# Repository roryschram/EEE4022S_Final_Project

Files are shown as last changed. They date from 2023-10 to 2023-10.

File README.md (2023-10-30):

## LoRa Based Communication System for Radiosonde Applications
### By Rory Schram

Welcome to my final year project GitHub page. This project focussed on the design and implementation of a LoRa-based radiosonde module for a weather balloon. Project files can be found in their respective folders, including all software, schematics, and PCB designs, for the transmission and receiver modules.

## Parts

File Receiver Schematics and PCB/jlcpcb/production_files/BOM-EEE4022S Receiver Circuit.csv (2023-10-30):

Comment | Designator | Footprint | LCSC
~ | U1 | ESP8266
~ | U4 | SX1278
Navigator Button | U2 | Push Button
~ | U5 | OLED Display

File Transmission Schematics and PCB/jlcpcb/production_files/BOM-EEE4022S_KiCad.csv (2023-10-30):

Comment | Designator | Footprint | LCSC
~ | U5 | FTDI
~ | U3 | NEO-6M
Left Button | U6 | Push Button
~ | U4 | BME280
Right Button | U7 | Push Button
~ | B1 | Battery HolderCharger
~ | U1 | STM32f4_Black_Pill
~ | U8 | OLED Display
~ | U2 | SX1278

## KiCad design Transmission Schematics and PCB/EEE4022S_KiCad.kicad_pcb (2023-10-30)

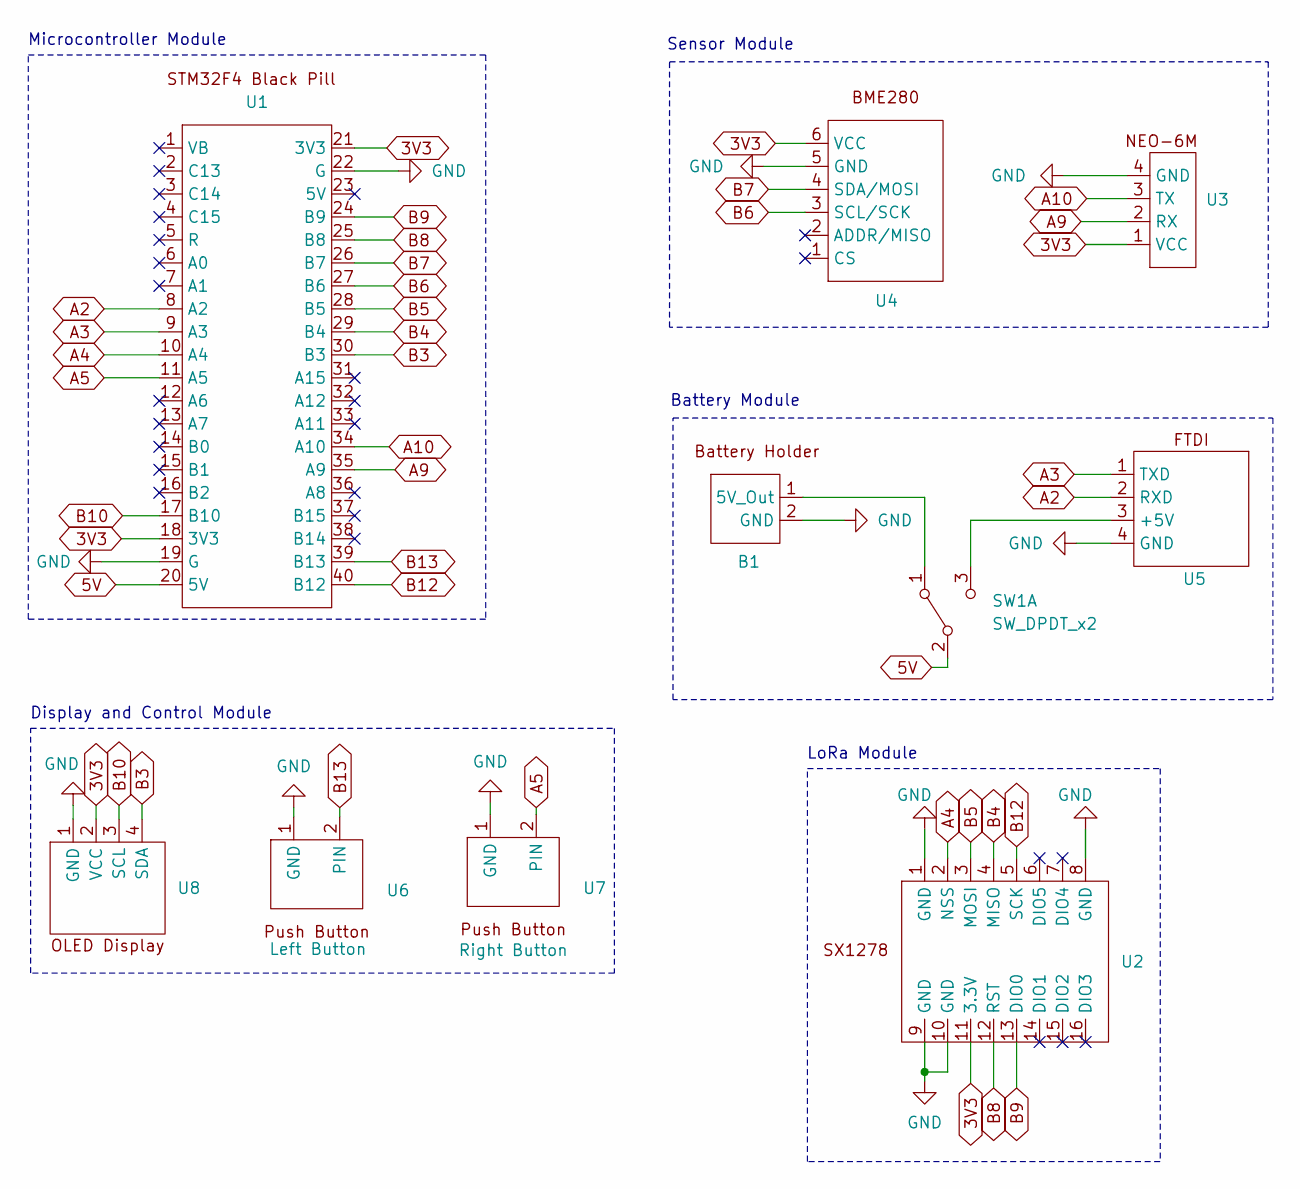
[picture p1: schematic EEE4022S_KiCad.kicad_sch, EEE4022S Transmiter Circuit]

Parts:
B1: Battery HolderCharger
SW1: SW_DPDT_x2
U1: STM32f4_Black_Pill
U2: SX1278
U3: NEO-6M
U4: BME280
U5: FTDI
U6: Left Button; Push Button
U7: Right Button; Push Button
U8: OLED Display

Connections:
3V3: U1.18 (3V3), U1.21 (3V3), U2.11 (3.3V), U3.1 (VCC), U4.6 (VCC), U8.2 (VCC)
5V: B1.1 (5V_Out), SW1.1 (A), SW1.2 (B), SW1.3 (C), U1.20 (5V), U5.3 (+5V)
A2: U1.8 (A2), U5.2 (RXD)
A3: U1.9 (A3), U5.1 (TXD)
A4: U1.10 (A4), U2.2 (NSS)
A5: U1.11 (A5), U7.2 (PIN)
A9: U1.35 (A9), U3.2 (RX)
A10: U1.34 (A10), U3.3 (TX)
B3: U1.30 (B3), U8.4 (SDA)
B4: U1.29 (B4), U2.4 (MISO)
B5: U1.28 (B5), U2.3 (MOSI)
B6: U1.27 (B6), U4.3 (SCL/SCK)
B7: U1.26 (B7), U4.4 (SDA/MOSI)
B8: U1.25 (B8), U2.12 (RST)
B9: U1.24 (B9), U2.13 (DIO0)
B10: U1.17 (B10), U8.3 (SCL)
B12: U1.40 (B12), U2.5 (SCK)
B13: U1.39 (B13), U6.2 (PIN)
GND: B1.2 (GND), U1.19 (G), U1.22 (G), U2.1 (GND), U2.8 (GND), U2.9 (GND), U2.10 (GND), U3.4 (GND), U4.5 (GND), U5.4 (GND), U6.1 (GND), U7.1 (GND), U8.1 (GND)

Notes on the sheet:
LoRa Module
Display and Control Module
Sensor Module
Microcontroller Module
Battery Module

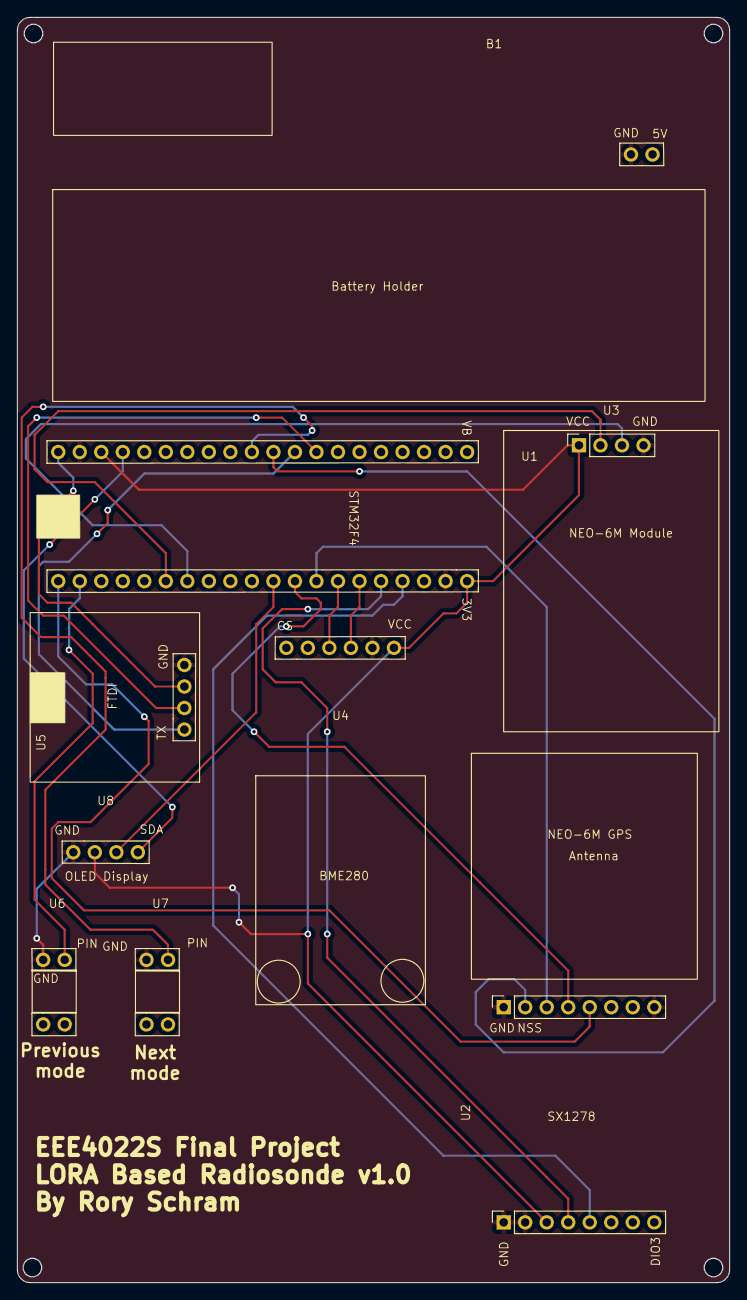
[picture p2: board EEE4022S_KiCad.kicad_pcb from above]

Board: 2 copper layers, 84.1 x 149.4 mm, 9 parts (0 on the bottom side), 19 nets.

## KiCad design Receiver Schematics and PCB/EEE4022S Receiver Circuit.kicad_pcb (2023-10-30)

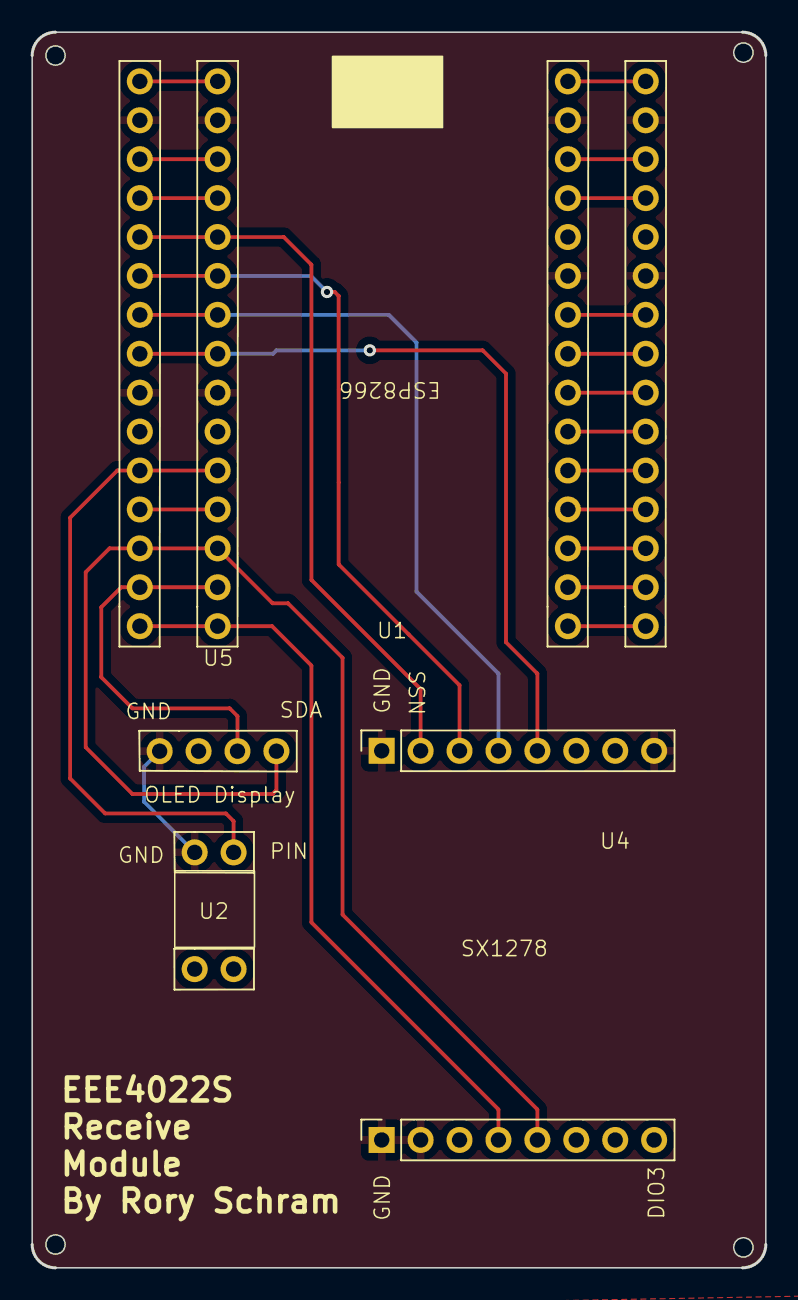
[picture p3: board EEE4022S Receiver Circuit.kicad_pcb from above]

Board: 2 copper layers, 47.9 x 80.6 mm, 4 parts (0 on the bottom side), 10 nets.

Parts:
U1: ESP8266
U2: Navigator Button; Push Button
U4: SX1278
U5: OLED Display

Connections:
3V3: U1.11 (3V3), U1.21 (3V3), U4.11 (3.3V), U5.2 (VCC)
D0: U1.16 (D0), U4.12 (RST)
D1: U1.17 (D1), U5.3 (SCL)
D2: U1.18 (D2), U4.13 (DIO0), U5.4 (SDA)
D4: U1.20 (D4), U2.2 (PIN)
D5: U1.23 (D5), U4.5 (SCK)
D6: U1.24 (D6), U4.4 (MISO)
D7: U1.25 (D7), U4.3 (MOSI)
D8: U1.26 (D8), U4.2 (NSS)
GND: U1.10 (GND), U1.14 (GND), U1.22 (GND), U1.29 (GND), U2.1 (GND), U4.1 (GND), U4.8 (GND), U4.9 (GND), U4.10 (GND), U5.1 (GND)

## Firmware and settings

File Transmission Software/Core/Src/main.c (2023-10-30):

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
/* Includes ------------------------------------------------------------------*/
#include "main.h"

/* USER CODE BEGIN Includes */
#include <stdio.h>
#include "minmea.h"
#include <stdlib.h>
#include <string.h>
#include <stdint.h>
#include "bmp280.h"
#include <float.h>
#include <math.h>
#include <LoRa.h>
#include "ssd1306.h"
#include "fonts.h"


/* USER CODE END Includes */

/* USER CODE BEGIN PD */
#define INDENT_SPACES "  "

/* USER CODE END PD */

I2C_HandleTypeDef hi2c1;
I2C_HandleTypeDef hi2c2;

SPI_HandleTypeDef hspi3;

TIM_HandleTypeDef htim3;

UART_HandleTypeDef huart1;
UART_HandleTypeDef huart2;

/* USER CODE BEGIN PV */
uint8_t gps_raw[512] = {"\0"};
uint8_t flag = 0;
char line[64] = {"\0"};
bool bme280p;
uint8_t transmit_data[256] = {"\0"};
LoRa myLoRa;
bool isLoraReady = true;
int preTicks = 0;
int currentTicks = 0;
int iMode = 1;
char sMode[10];
bool bModeChanged = true;
bool sendData = false;


bool beginTransmit = false;
uint16_t packetSize = 0;

//Variables to work out altitude

//Pressure at sea level
float P_b = 101325;

//Height that we are calculating
float altitude = 0;


BMP280_HandleTypedef bmp280;

float pressure, temperature, humidity;
char sPressure[128] = {"\0"};
char sTemperature[128] = {"\0"};
char sHumidity[128] = {"\0"};
char sAltitude[128] = {"\0"};

size_t size;
uint8_t Data[256] = {"\0"};


/* USER CODE END PV */

void SystemClock_Config(void);
static void MX_GPIO_Init(void);
static void MX_USART1_UART_Init(void);
static void MX_USART2_UART_Init(void);
static void MX_I2C1_Init(void);
static void MX_SPI3_Init(void);
static void MX_I2C2_Init(void);
static void MX_TIM3_Init(void);
/* USER CODE BEGIN PFP */
uint16_t buildDataPacket();


/* USER CODE END PFP */

/**
  * @brief  The application entry point.
  * @retval int
  */
int main(void)
{
  /* MCU Configuration--------------------------------------------------------*/

  /* Reset of all peripherals, Initializes the Flash interface and the Systick. */
  HAL_Init();

  /* Configure the system clock */
  SystemClock_Config();

  /* Initialize all configured peripherals */
  MX_GPIO_Init();
  MX_USART1_UART_Init();
  MX_USART2_UART_Init();
  MX_I2C1_Init();
  MX_SPI3_Init();
  MX_I2C2_Init();
  MX_TIM3_Init();
  /* USER CODE BEGIN 2 */
  
  // Start timer
  HAL_TIM_Base_Start_IT(&htim3);

  bmp280_init_default_params(&bmp280.params);
	bmp280.addr = 0x77;
	bmp280.i2c = &hi2c1;

	while (!bmp280_init(&bmp280, &bmp280.params)) {
		size = sprintf((char *)Data, "BMP280 initialization failed\n");
		HAL_UART_Transmit(&huart2, Data, size, 1000);
		HAL_Delay(2000);
	}
	bool bme280p = bmp280.id == BME280_CHIP_ID;
	size = sprintf((char *)Data, "\nBMP280: found %s\n", bme280p ? "BME280" : "BMP280");
	HAL_UART_Transmit(&huart2, Data, size, 1000);

  myLoRa = newLoRa();
  myLoRa.CS_port         = GPIOA;
  myLoRa.CS_pin          = GPIO_PIN_4;
  myLoRa.reset_port      = GPIOB;
  myLoRa.reset_pin       = GPIO_PIN_8;
  myLoRa.DIO0_port       = GPIOB;
  myLoRa.DIO0_pin        = GPIO_PIN_9;
  myLoRa.hSPIx           = &hspi3;
  
  
  myLoRa.frequency             = 433;             // default = 433 MHz
  myLoRa.spreadingFactor        = SF_7;            // default = SF_7
  myLoRa.bandWidth             = BW_7_8KHz;       // default = BW_125KHz
  myLoRa.crcRate               = CR_4_5;          // default = CR_4_5
  myLoRa.power                 = POWER_20db;      // default = 20db
  myLoRa.overCurrentProtection = 100;             // default = 100 mA
  myLoRa.preamble              = 8;              // default = 8;

  uint16_t ret = LoRa_init(&myLoRa);
  uint8_t buff[128] = {"\0"};
  

if (ret==LORA_OK){
  snprintf(buff,sizeof(buff),"LoRa is running... :) \n\r");
  size = strlen(&buff);
  LoRa_transmit(&myLoRa, (uint8_t*)buff, size, 100);
  HAL_UART_Transmit_IT(&huart2, buff, size);
}
else{
  snprintf(buff,sizeof(buff),"\n\r LoRa failed :( \n\r Error code: %d \n\r", ret);
  size = strlen(&buff);
  HAL_UART_Transmit_IT(&huart2, buff, size);
}


ssd1306_Init(&hi2c2);

// Set cursors and write the word "mode"
ssd1306_SetCursor(0, 0);
ssd1306_WriteString("Mode:", Font_16x26, White);

ssd1306_SetCursor(0, 35);
sprintf(sMode, "%d", iMode);
ssd1306_WriteString(sMode, Font_16x26, White);

// Copy all data from local screenbuffer to the screen
ssd1306_UpdateScreen(&hi2c2);

HAL_UARTEx_ReceiveToIdle(&huart1,(uint8_t*)gps_raw,512,512,1000);


  /* USER CODE END 2 */

  /* Infinite loop */
  /* USER CODE BEGIN WHILE */
  while (1)
  {


    if (beginTransmit) {
      //HAL_UART_Transmit(&huart2,(uint8_t *)gps_raw,512, 1000);
      //HAL_UARTEx_ReceiveToIdle_IT(&huart1,(uint8_t*)gps_raw,512);
      packetSize = buildDataPacket();
      
      size = strlen(&transmit_data);
      ret = LoRa_transmit(&myLoRa, (uint8_t*)transmit_data, packetSize, 10000);
      memset(transmit_data, '\0', sizeof(transmit_data));

      // sprintf(transmit_data, "Data sent with code %u\n", ret);
      // size = strlen(&transmit_data);
	    // HAL_UART_Transmit(&huart2, (uint8_t *)transmit_data, size, 1000);
      // memset(transmit_data, '\0', sizeof(transmit_data));
      
      beginTransmit = false;
    }      

    if (bModeChanged) {
switch (iMode) {
    case 1:
      // statements
      myLoRa.frequency             = 433;             // default = 433 MHz
      myLoRa.spreadingFactor        = SF_7;            // default = SF_7
      myLoRa.bandWidth             = BW_7_8KHz;       // default = BW_125KHz
      myLoRa.crcRate               = CR_4_5;          // default = CR_4_5
      myLoRa.power                 = POWER_20db;      // default = 20db
      myLoRa.overCurrentProtection = 100;             // default = 100 mA
      myLoRa.preamble              = 8;              // default = 8;
      LoRa_init(&myLoRa);
      break;

    case 2:
      // statements
      myLoRa.frequency             = 433;             // default = 433 MHz
      myLoRa.spreadingFactor        = SF_7;            // default = SF_7
      myLoRa.bandWidth             = BW_10_4KHz;       // default = BW_125KHz
      myLoRa.crcRate               = CR_4_5;          // default = CR_4_5
      myLoRa.power                 = POWER_20db;      // default = 20db
      myLoRa.overCurrentProtection = 100;             // default = 100 mA
      myLoRa.preamble              = 8;              // default = 8;
      LoRa_init(&myLoRa);
      break;

    case 3:
      // statements
      myLoRa.frequency             = 433;             // default = 433 MHz
      myLoRa.spreadingFactor        = SF_7;            // default = SF_7
      myLoRa.bandWidth             = BW_15_6KHz;       // default = BW_125KHz
      myLoRa.crcRate               = CR_4_5;          // default = CR_4_5
      myLoRa.power                 = POWER_20db;      // default = 20db
      myLoRa.overCurrentProtection = 100;             // default = 100 mA
      myLoRa.preamble              = 8;              // default = 8;
      LoRa_init(&myLoRa);
      break;

    case 4:
      // statements
      myLoRa.frequency             = 433;             // default = 433 MHz
      myLoRa.spreadingFactor        = SF_7;            // default = SF_7
      myLoRa.bandWidth             = BW_20_8KHz;       // default = BW_125KHz
      myLoRa.crcRate               = CR_4_5;          // default = CR_4_5
      myLoRa.power                 = POWER_20db;      // default = 20db
      myLoRa.overCurrentProtection = 100;             // default = 100 mA
      myLoRa.preamble              = 8;              // default = 8;
      LoRa_init(&myLoRa);
      break;

    case 5:
      // statements
      myLoRa.frequency             = 433;             // default = 433 MHz
      myLoRa.spreadingFactor        = SF_7;            // default = SF_7
      myLoRa.bandWidth             = BW_31_25KHz;       // default = BW_125KHz
      myLoRa.crcRate               = CR_4_5;          // default = CR_4_5
      myLoRa.power                 = POWER_20db;      // default = 20db
      myLoRa.overCurrentProtection = 100;             // default = 100 mA
      myLoRa.preamble              = 8;              // default = 8;
      LoRa_init(&myLoRa);
      break;

    case 6:
      // statements
      myLoRa.frequency             = 433;             // default = 433 MHz
      myLoRa.spreadingFactor        = SF_7;            // default = SF_7
      myLoRa.bandWidth             = BW_41_7KHz;       // default = BW_125KHz
      myLoRa.crcRate               = CR_4_5;          // default = CR_4_5
      myLoRa.power                 = POWER_20db;      // default = 20db
      myLoRa.overCurrentProtection = 100;             // default = 100 mA
      myLoRa.preamble              = 8;              // default = 8;
      LoRa_init(&myLoRa);
      break;

    case 7:
      // statements
      myLoRa.frequency             = 433;             // default = 433 MHz
      myLoRa.spreadingFactor        = SF_7;            // default = SF_7
      myLoRa.bandWidth             = BW_62_5KHz;       // default = BW_125KHz
      myLoRa.crcRate               = CR_4_5;          // default = CR_4_5
      myLoRa.power                 = POWER_20db;      // default = 20db
      myLoRa.overCurrentProtection = 100;             // default = 100 mA
      myLoRa.preamble              = 8;              // default = 8;
      LoRa_init(&myLoRa);
      break;

    case 8:
      // statements
      myLoRa.frequency             = 433;             // default = 433 MHz
      myLoRa.spreadingFactor        = SF_7;            // default = SF_7
      myLoRa.bandWidth             = BW_125KHz;       // default = BW_125KHz
      myLoRa.crcRate               = CR_4_5;          // default = CR_4_5
      myLoRa.power                 = POWER_20db;      // default = 20db
      myLoRa.overCurrentProtection = 100;             // default = 100 mA
      myLoRa.preamble              = 8;              // default = 8;
      LoRa_init(&myLoRa);
      break;

    case 9:
      // statements
      myLoRa.frequency             = 433;             // default = 433 MHz
      myLoRa.spreadingFactor        = SF_7;            // default = SF_7
      myLoRa.bandWidth             = BW_250KHz;       // default = BW_125KHz
      myLoRa.crcRate               = CR_4_5;          // default = CR_4_5
      myLoRa.power                 = POWER_20db;      // default = 20db
      myLoRa.overCurrentProtection = 100;             // default = 100 mA
      myLoRa.preamble              = 8;              // default = 8;
      LoRa_init(&myLoRa);
      break;

    case 10:
      // statements
      myLoRa.frequency             = 433;             // default = 433 MHz
      myLoRa.spreadingFactor        = SF_7;            // default = SF_7
      myLoRa.bandWidth             = BW_500KHz;       // default = BW_125KHz
      myLoRa.crcRate               = CR_4_5;          // default = CR_4_5
      myLoRa.power                 = POWER_20db;      // default = 20db
      myLoRa.overCurrentProtection = 100;             // default = 100 mA
      myLoRa.preamble              = 8;              // default = 8;
      LoRa_init(&myLoRa);
      break;
    
    case 11:
      // statements
      myLoRa.frequency             = 433;             // default = 433 MHz
      myLoRa.spreadingFactor        = SF_8;            // default = SF_7
      myLoRa.bandWidth             = BW_7_8KHz;       // default = BW_125KHz
      myLoRa.crcRate               = CR_4_5;          // default = CR_4_5
      myLoRa.power                 = POWER_20db;      // default = 20db
      myLoRa.overCurrentProtection = 100;             // default = 100 mA
      myLoRa.preamble              = 8;              // default = 8;
      LoRa_init(&myLoRa);
      break;

    case 12:
      // statements
      myLoRa.frequency             = 433;             // default = 433 MHz
      myLoRa.spreadingFactor        = SF_8;            // default = SF_7
      myLoRa.bandWidth             = BW_10_4KHz;       // default = BW_125KHz
      myLoRa.crcRate               = CR_4_5;          // default = CR_4_5
      myLoRa.power                 = POWER_20db;      // default = 20db
      myLoRa.overCurrentProtection = 100;             // default = 100 mA
      myLoRa.preamble              = 8;              // default = 8;
      LoRa_init(&myLoRa);
      break;

    case 13:
      // statements
      myLoRa.frequency             = 433;             // default = 433 MHz
      myLoRa.spreadingFactor        = SF_8;            // default = SF_7
      myLoRa.bandWidth             = BW_15_6KHz;       // default = BW_125KHz
      myLoRa.crcRate               = CR_4_5;          // default = CR_4_5
      myLoRa.power                 = POWER_20db;      // default = 20db
      myLoRa.overCurrentProtection = 100;             // default = 100 mA
      myLoRa.preamble              = 8;              // default = 8;
      LoRa_init(&myLoRa);
      break;

    case 14:
      // statements
      myLoRa.frequency             = 433;             // default = 433 MHz
      myLoRa.spreadingFactor        = SF_8;            // default = SF_7
      myLoRa.bandWidth             = BW_20_8KHz;       // default = BW_125KHz
      myLoRa.crcRate               = CR_4_5;          // default = CR_4_5
      myLoRa.power                 = POWER_20db;      // default = 20db
      myLoRa.overCurrentProtection = 100;             // default = 100 mA
      myLoRa.preamble              = 8;              // default = 8;
      LoRa_init(&myLoRa);
      break;

    case 15:
      // statements
      myLoRa.frequency             = 433;             // default = 433 MHz
      myLoRa.spreadingFactor        = SF_8;            // default = SF_7
      myLoRa.bandWidth             = BW_31_25KHz;       // default = BW_125KHz
      myLoRa.crcRate               = CR_4_5;          // default = CR_4_5
      myLoRa.power                 = POWER_20db;      // default = 20db
      myLoRa.overCurrentProtection = 100;             // default = 100 mA
      myLoRa.preamble              = 8;              // default = 8;
      LoRa_init(&myLoRa);
      break;

    case 16:
      // statements
      myLoRa.frequency             = 433;             // default = 433 MHz
      myLoRa.spreadingFactor        = SF_8;            // default = SF_7
      myLoRa.bandWidth             = BW_41_7KHz;       // default = BW_125KHz
      myLoRa.crcRate               = CR_4_5;          // default = CR_4_5
      myLoRa.power                 = POWER_20db;      // default = 20db
      myLoRa.overCurrentProtection = 100;             // default = 100 mA
      myLoRa.preamble              = 8;              // default = 8;
      LoRa_init(&myLoRa);
      break;

    case 17:
      // statements
      myLoRa.frequency             = 433;             // default = 433 MHz
      myLoRa.spreadingFactor        = SF_8;            // default = SF_7
      myLoRa.bandWidth             = BW_62_5KHz;       // default = BW_125KHz
      myLoRa.crcRate               = CR_4_5;          // default = CR_4_5
      myLoRa.power                 = POWER_20db;      // default = 20db
      myLoRa.overCurrentProtection = 100;             // default = 100 mA
      myLoRa.preamble              = 8;              // default = 8;
      LoRa_init(&myLoRa);
      break;

    case 18:
      // statements
      myLoRa.frequency             = 433;             // default = 433 MHz
      myLoRa.spreadingFactor        = SF_8;            // default = SF_7
      myLoRa.bandWidth             = BW_125KHz;       // default = BW_125KHz
      myLoRa.crcRate               = CR_4_5;          // default = CR_4_5
      myLoRa.power                 = POWER_20db;      // default = 20db
      myLoRa.overCurrentProtection = 100;             // default = 100 mA
      myLoRa.preamble              = 8;              // default = 8;
      LoRa_init(&myLoRa);
      break;

    case 19:
      // statements
      myLoRa.frequency             = 433;             // default = 433 MHz
      myLoRa.spreadingFactor        = SF_8;            // default = SF_7
      myLoRa.bandWidth             = BW_250KHz;       // default = BW_125KHz
      myLoRa.crcRate               = CR_4_5;          // default = CR_4_5
      myLoRa.power                 = POWER_20db;      // default = 20db
      myLoRa.overCurrentProtection = 100;             // default = 100 mA
      myLoRa.preamble              = 8;              // default = 8;
      LoRa_init(&myLoRa);
      break;

    case 20:
      // statements
      myLoRa.frequency             = 433;             // default = 433 MHz
      myLoRa.spreadingFactor        = SF_8;            // default = SF_7
      myLoRa.bandWidth             = BW_500KHz;       // default = BW_125KHz
      myLoRa.crcRate               = CR_4_5;          // default = CR_4_5
      myLoRa.power                 = POWER_20db;      // default = 20db
      myLoRa.overCurrentProtection = 100;             // default = 100 mA
      myLoRa.preamble              = 8;              // default = 8;
      LoRa_init(&myLoRa);
      break;

    case 21:
      // statements
      myLoRa.frequency             = 433;             // default = 433 MHz
      myLoRa.spreadingFactor        = SF_9;            // default = SF_7
      myLoRa.bandWidth             = BW_7_8KHz;       // default = BW_125KHz
      myLoRa.crcRate               = CR_4_5;          // default = CR_4_5
      myLoRa.power                 = POWER_20db;      // default = 20db
      myLoRa.overCurrentProtection = 100;             // default = 100 mA
      myLoRa.preamble              = 8;              // default = 8;
      LoRa_init(&myLoRa);
      break;

    case 22:
      // statements
      myLoRa.frequency             = 433;             // default = 433 MHz
      myLoRa.spreadingFactor        = SF_9;            // default = SF_7
      myLoRa.bandWidth             = BW_10_4KHz;       // default = BW_125KHz
      myLoRa.crcRate               = CR_4_5;          // default = CR_4_5
      myLoRa.power                 = POWER_20db;      // default = 20db
      myLoRa.overCurrentProtection = 100;             // default = 100 mA
      myLoRa.preamble              = 8;              // default = 8;
      LoRa_init(&myLoRa);
      break;

    case 23:
      // statements
      myLoRa.frequency             = 433;             // default = 433 MHz
      myLoRa.spreadingFactor        = SF_9;            // default = SF_7
      myLoRa.bandWidth             = BW_15_6KHz;       // default = BW_125KHz
      myLoRa.crcRate               = CR_4_5;          // default = CR_4_5
      myLoRa.power                 = POWER_20db;      // default = 20db
      myLoRa.overCurrentProtection = 100;             // default = 100 mA
      myLoRa.preamble              = 8;              // default = 8;
      LoRa_init(&myLoRa);
      break;

    case 24:
      // statements
      myLoRa.frequency             = 433;             // default = 433 MHz
      myLoRa.spreadingFactor        = SF_9;            // default = SF_7
      myLoRa.bandWidth             = BW_20_8KHz;       // default = BW_125KHz
      myLoRa.crcRate               = CR_4_5;          // default = CR_4_5
      myLoRa.power                 = POWER_20db;      // default = 20db
      myLoRa.overCurrentProtection = 100;             // default = 100 mA
      myLoRa.preamble              = 8;              // default = 8;
      LoRa_init(&myLoRa);
      break;

    case 25:
      // statements
      myLoRa.frequency             = 433;             // default = 433 MHz
      myLoRa.spreadingFactor        = SF_9;            // default = SF_7
      myLoRa.bandWidth             = BW_31_25KHz;       // default = BW_125KHz
      myLoRa.crcRate               = CR_4_5;          // default = CR_4_5
      myLoRa.power                 = POWER_20db;      // default = 20db
      myLoRa.overCurrentProtection = 100;             // default = 100 mA
      myLoRa.preamble              = 8;              // default = 8;
      LoRa_init(&myLoRa);
      break;

    case 26:
      // statements
      myLoRa.frequency             = 433;             // default = 433 MHz
      myLoRa.spreadingFactor        = SF_9;            // default = SF_7
      myLoRa.bandWidth             = BW_41_7KHz;       // default = BW_125KHz
      myLoRa.crcRate               = CR_4_5;          // default = CR_4_5
      myLoRa.power                 = POWER_20db;      // default = 20db
      myLoRa.overCurrentProtection = 100;             // default = 100 mA
      myLoRa.preamble              = 8;              // default = 8;
      LoRa_init(&myLoRa);
      break;

    case 27:
      // statements
      myLoRa.frequency             = 433;             // default = 433 MHz
      myLoRa.spreadingFactor        = SF_9;            // default = SF_7
      myLoRa.bandWidth             = BW_62_5KHz;       // default = BW_125KHz
      myLoRa.crcRate               = CR_4_5;          // default = CR_4_5
      myLoRa.power                 = POWER_20db;      // default = 20db
      myLoRa.overCurrentProtection = 100;             // default = 100 mA
      myLoRa.preamble              = 8;              // default = 8;
      LoRa_init(&myLoRa);
      break;

    case 28:
      // statements
      myLoRa.frequency             = 433;             // default = 433 MHz
      myLoRa.spreadingFactor        = SF_9;            // default = SF_7
      myLoRa.bandWidth             = BW_125KHz;       // default = BW_125KHz
      myLoRa.crcRate               = CR_4_5;          // default = CR_4_5
      myLoRa.power                 = POWER_20db;      // default = 20db
      myLoRa.overCurrentProtection = 100;             // default = 100 mA
      myLoRa.preamble              = 8;              // default = 8;
      LoRa_init(&myLoRa);
      break;
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

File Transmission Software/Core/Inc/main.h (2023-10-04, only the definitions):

#define rightButton_Pin GPIO_PIN_5
#define rightButton_GPIO_Port GPIOA
#define rightButton_EXTI_IRQn EXTI9_5_IRQn
#define leftButton_Pin GPIO_PIN_13
#define leftButton_GPIO_Port GPIOB
#define leftButton_EXTI_IRQn EXTI15_10_IRQn

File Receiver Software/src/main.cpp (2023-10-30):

#include <SPI.h>
#include <LoRa.h>
#include <Adafruit_GFX.h>
#include "ssd1306.h"
#include "driver/gpio.h"

#define ss 5
#define rst 14
#define dio0 2

int iMode = 1;
char sMode[10] = "1";
unsigned long currentTicks = 0;  // current time
unsigned long preTicks = 0;    // previous time that button was pushed
unsigned long delayDebounce = 200;    // Delay to be adheared to for the debouncing
bool leftButton = false;
bool rightButton = false;
bool bModeChanged = true;
int iTotalRSSI = 0;
int iCountRSSI = 0;
float fAveRSSI = 0.0;

void IRAM_ATTR leftButtonPush();
void IRAM_ATTR rightButtonPush();

void setup() {
  Serial.begin(115200);
  while (!Serial);
  Serial.println("LoRa Receiver");

  LoRa.setPins(ss, rst, dio0);
  if (!LoRa.begin(433e6)) {
    Serial.println("Starting LoRa failed!");
    while (1);
  }
  
  LoRa.setSpreadingFactor(7);
  LoRa.setSignalBandwidth(7.8E3);
  LoRa.setCodingRate4(5);
  LoRa.setPreambleLength(8);
  LoRa.setGain(1);

  // put the radio into receive mode
  LoRa.receive();

  pinMode(15, INPUT_PULLUP); // Left button input
  pinMode(0, INPUT_PULLUP); // Right button input
  attachInterrupt(15, leftButtonPush, FALLING);
  attachInterrupt(0, rightButtonPush, FALLING);


  ssd1306_128x64_i2c_init();
  ssd1306_fillScreen(0x00);
  ssd1306_setFixedFont(ssd1306xled_font6x8);
  ssd1306_printFixedN(0,  0, "Mode:", STYLE_NORMAL, FONT_SIZE_4X);
  sprintf(sMode, "%d        ",iMode);
  ssd1306_printFixedN(0,  35, sMode, STYLE_NORMAL, FONT_SIZE_4X);
  //Serial.println(getXtalFrequencyMhz());
  //Serial.println(getCpuFrequencyMhz());
}

void loop() {
  // try to parse packet
  int packetSize = LoRa.parsePacket();
  if (packetSize) {
    iCountRSSI += 1;
    // received a packet
    Serial.print("Received packet '");
    // read packet
    while (LoRa.available()) {
      Serial.print((char)LoRa.read());
    }
    
    // print RSSI of packet
    Serial.print("' with RSSI ");
    Serial.print(LoRa.packetRssi());
    iTotalRSSI += LoRa.packetRssi();
    Serial.print(" and frequency error of ");
    Serial.println(LoRa.packetFrequencyError());
  }

  if (leftButton) {
    if (iCountRSSI>0) {
      fAveRSSI = float(iTotalRSSI)/float(iCountRSSI);
      Serial.printf("Average RSSI: %.2f\n",fAveRSSI);
      fAveRSSI = 0.0;
      iTotalRSSI = 0;
      iCountRSSI = 0;
    }

    Serial.println("");

    if (iMode == 1) {
      iMode = 60;
      sprintf(sMode, "%d        ",iMode);
      ssd1306_printFixedN(0,  35, sMode, STYLE_NORMAL, FONT_SIZE_4X);
    } else {
      iMode = iMode - 1;
      sprintf(sMode, "%d        ",iMode);
      ssd1306_printFixedN(0,  35, sMode, STYLE_NORMAL, FONT_SIZE_4X);
    }


    leftButton = false;
  }

  if (rightButton) {
    if (iCountRSSI>0) {
      fAveRSSI = float(iTotalRSSI)/float(iCountRSSI);
      Serial.printf("Average RSSI: %.2f\n",fAveRSSI);
      fAveRSSI = 0.0;
      iTotalRSSI = 0;
      iCountRSSI = 0;
    }


    Serial.println("");

    if (iMode == 60) {
      iMode = 1;
      sprintf(sMode, "%d        ",iMode);
      ssd1306_printFixedN(0,  35, sMode, STYLE_NORMAL, FONT_SIZE_4X);
    } else {
      iMode = iMode + 1;
      sprintf(sMode, "%d        ",iMode);
      ssd1306_printFixedN(0,  35, sMode, STYLE_NORMAL, FONT_SIZE_4X);
    }
    rightButton = false;
  }


  if (bModeChanged){
    switch (iMode)
    {
    case 1:
      LoRa.setSpreadingFactor(7);
      LoRa.setSignalBandwidth(7.8E3);
      LoRa.setCodingRate4(5);
      LoRa.setPreambleLength(8);
      break;

    case 2:
      LoRa.setSpreadingFactor(7);
      LoRa.setSignalBandwidth(10.4E3);
      LoRa.setCodingRate4(5);
      LoRa.setPreambleLength(8);
      break;

    case 3:
      LoRa.setSpreadingFactor(7);
      LoRa.setSignalBandwidth(15.6E3);
      LoRa.setCodingRate4(5);
      LoRa.setPreambleLength(8);
      break;

    case 4:
      LoRa.setSpreadingFactor(7);
      LoRa.setSignalBandwidth(20.8E3);
      LoRa.setCodingRate4(5);
      LoRa.setPreambleLength(8);
      break;

    case 5:
      LoRa.setSpreadingFactor(7);
      LoRa.setSignalBandwidth(31.25E3);
      LoRa.setCodingRate4(5);
      LoRa.setPreambleLength(8);
      break;

    case 6:
      LoRa.setSpreadingFactor(7);
      LoRa.setSignalBandwidth(41.7E3);
      LoRa.setCodingRate4(5);
      LoRa.setPreambleLength(8);
      break;

    case 7:
      LoRa.setSpreadingFactor(7);
      LoRa.setSignalBandwidth(62.5E3);
      LoRa.setCodingRate4(5);
      LoRa.setPreambleLength(8);
      break;

    case 8:
      LoRa.setSpreadingFactor(7);
      LoRa.setSignalBandwidth(125E3);
      LoRa.setCodingRate4(5);
      LoRa.setPreambleLength(8);
      break;

    case 9:
      LoRa.setSpreadingFactor(7);
      LoRa.setSignalBandwidth(250E3);
      LoRa.setCodingRate4(5);
      LoRa.setPreambleLength(8);
      break;

    case 10:
      LoRa.setSpreadingFactor(7);
      LoRa.setSignalBandwidth(500E3);
      LoRa.setCodingRate4(5);
      LoRa.setPreambleLength(8);
      break;

    case 11:
      LoRa.setSpreadingFactor(8);
      LoRa.setSignalBandwidth(7.8E3);
      LoRa.setCodingRate4(5);
      LoRa.setPreambleLength(8);
      break;

    case 12:
      LoRa.setSpreadingFactor(8);
      LoRa.setSignalBandwidth(10.4E3);
      LoRa.setCodingRate4(5);
      LoRa.setPreambleLength(8);
      break;

    case 13:
      LoRa.setSpreadingFactor(8);
      LoRa.setSignalBandwidth(15.6E3);
      LoRa.setCodingRate4(5);
      LoRa.setPreambleLength(8);
      break;

    case 14:
      LoRa.setSpreadingFactor(8);
      LoRa.setSignalBandwidth(20.8E3);
      LoRa.setCodingRate4(5);
      LoRa.setPreambleLength(8);
      break;

    case 15:
      LoRa.setSpreadingFactor(8);
      LoRa.setSignalBandwidth(31.25E3);
      LoRa.setCodingRate4(5);
      LoRa.setPreambleLength(8);
      break;

    case 16:
      LoRa.setSpreadingFactor(8);
      LoRa.setSignalBandwidth(41.7E3);
      LoRa.setCodingRate4(5);
      LoRa.setPreambleLength(8);
      break;

    case 17:
      LoRa.setSpreadingFactor(8);
      LoRa.setSignalBandwidth(62.5E3);
      LoRa.setCodingRate4(5);
      LoRa.setPreambleLength(8);
      break;

    case 18:
      LoRa.setSpreadingFactor(8);
      LoRa.setSignalBandwidth(125E3);
      LoRa.setCodingRate4(5);
      LoRa.setPreambleLength(8);
      break;

    case 19:
      LoRa.setSpreadingFactor(8);
      LoRa.setSignalBandwidth(250E3);
      LoRa.setCodingRate4(5);
      LoRa.setPreambleLength(8);
      break;

    case 20:
      LoRa.setSpreadingFactor(8);
      LoRa.setSignalBandwidth(500E3);
      LoRa.setCodingRate4(5);
      LoRa.setPreambleLength(8);
      break;

    case 21:
      LoRa.setSpreadingFactor(9);
      LoRa.setSignalBandwidth(7.8E3);
      LoRa.setCodingRate4(5);
      LoRa.setPreambleLength(8);
      break;

    case 22:
      LoRa.setSpreadingFactor(9);
      LoRa.setSignalBandwidth(10.4E3);
      LoRa.setCodingRate4(5);
      LoRa.setPreambleLength(8);
      break;
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

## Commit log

2023-09-27 Fixed Lora Mdule with reset low issue
    [eee4022s.ioc, main.c]
2023-10-05 Working System, now working on a timer
2023-10-30 More cleaning up
    [BOM-EEE4022S Receiver Circuit.csv, BOM-EEE4022S_KiCad.csv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]

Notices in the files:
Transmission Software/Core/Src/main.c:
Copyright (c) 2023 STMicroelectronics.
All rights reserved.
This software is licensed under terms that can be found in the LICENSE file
